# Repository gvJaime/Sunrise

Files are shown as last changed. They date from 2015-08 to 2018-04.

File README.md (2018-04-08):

# Sunrise Project

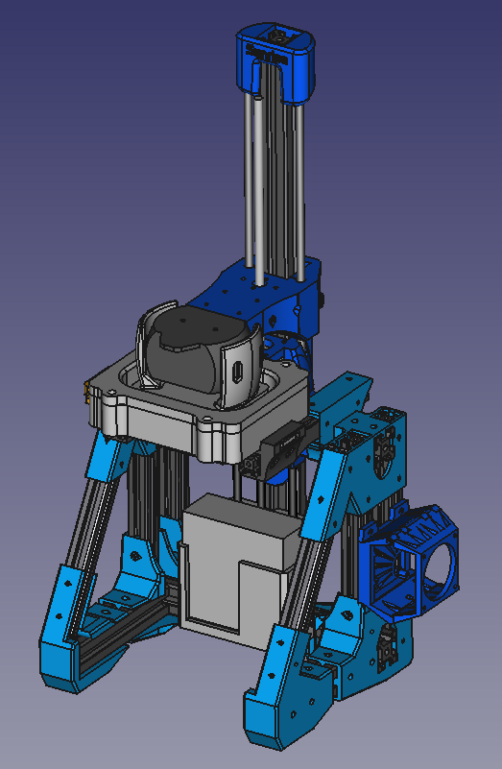
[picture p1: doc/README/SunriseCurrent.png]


## Introduction

The Sunrise Project is a research project, that aims to design an Open Source  hackable DLP based 3D printing system.

## Approach
The intention is to make the machine accesible to the general public. It must be sourceable, craftable, and modifiable by everyone. It aspires to be a platform for the community to explore this technology. Mechanics are scalable, source is available and modifiable, tools are open and obtainable.

## The technology

DLP 3D Printing uses photopolymierizing resin to craft the parts. Parts generate layer by layer as they are cured by a projector that outputs the cross-sections of the part, into the resin. There are various mechanical structures that can be used to achieve this.

This machine has what is called a _Bottom-Up_ structure. It has a vat, with transparent bottom, filled with resin. Underneath, an upward pointing DLP projector shoots light through the bottom window. The light striking on a **downward pointing** build surface cures the resin, forming a new layer.
Repeating this process, curing one layer below the previous one, ends up crafting the whole part, **upside down**.

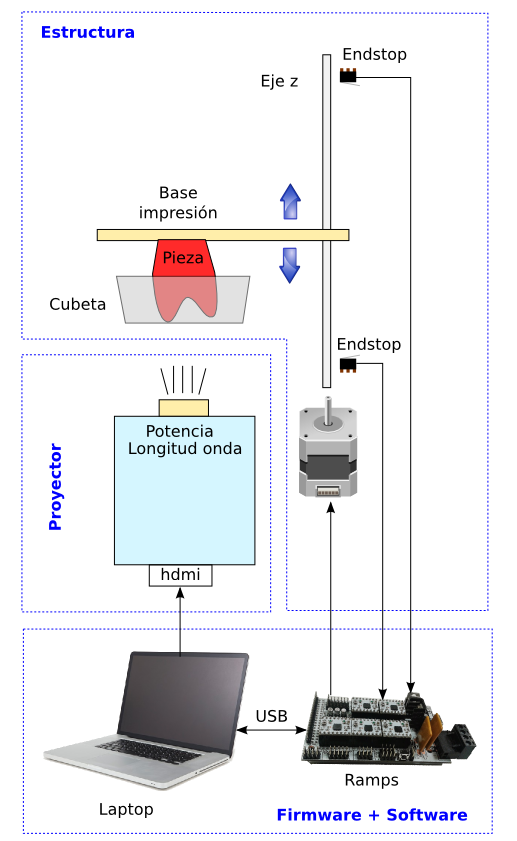
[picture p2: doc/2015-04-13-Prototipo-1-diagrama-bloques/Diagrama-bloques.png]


## The machine

This machine tries to stick to the RepRap philosophy, so structure and moving parts are 3D printed. Motion control is performed by an Arduino with a CNCShield, running a version of [GRBL][GRBL-link] that can be found [here][Sunrise-fw].
The projector is an [Optoma ML750][Optoma-link], with hacked optics for nearer focus.
PDMS based vat and flexible bottom vat system are being considered.

## About this repo

This repo contains the mechanical structure source. The tool of use is FreeCAD.
Folder content is descripted below
* `src`: Source files and assembly.
* `Step`: Step files for CAD import.
* `stl`: stl files for 3D printing.
* `FEM`: Part file duplicates for possible FEM analysis.
* `Fonts`: Fonts used in the design of the parts.
* `doc`: useful files for documentation
* `Software`: Provisional, holds useful software until it gets big enough for it to have its own repo.

### Cloning this machine

To build this machine, you need to print the 3D printable parts in [the stl folder][stlfolder]. You need to print each file once.

You will also need:
* 1958 mm of 20x20 aluminium extrusion profile
* 1378 mm of 30x30 aluminium extrusion profile
* Smooth rods, depending on desired Zaxis length
* Hammerhead nuts (Around 196 for 20x20 profiles and 52 for 30x30)
* DIN912 M4x8 bolts for 20x20 hammerhead nuts
* DIN912 M6x10 bolts for 30x30 hammerhead nuts
* 2 M3x10 Bolts
* 1 M3x20 Bolt
* 1 M3x30 Bolt
* A hacked Optoma ML750 (Focus moved forward with a M2 nut)

The length of the pieces of aluminium profiles and smooth rods can be seen in the [assembly file][Assembly]. Due to this being still in development there's not a lot of documentation. If you have any doubts [feel free to ask in the "issues" section][issue].

**Please note:** From v0.2.5 this repo uses [Assembly 2 FreeCAD workbench][Assembly2] for the assembly. You may want to install it before opening the assembly file.

### Contributing to this repo

You can contribute to this repo by forking it, and making pull requests to the [Development branch][Develop]. If you find problems to make the contribution this way, [place an issue][issue] and we'll work it out.

Due to FCStd files being unmergeable, Assembly.FCStd is modified only on the Development branch. It may not be included in pull requests. Remember that you need [Assembly 2 FreeCAD workbench][Assembly2] to open it.

In case of contributing using gitflow, take advantage of git diff features on FCStd files, and avoid big commit files, paste this lines on your ~/.git/config:
```
[include]
    path = ../.gitconfig
```
These will include the particular repo configuration, that tells git to unzip the files before diffing them.

## History

### Sunrise v0.3 (In development)

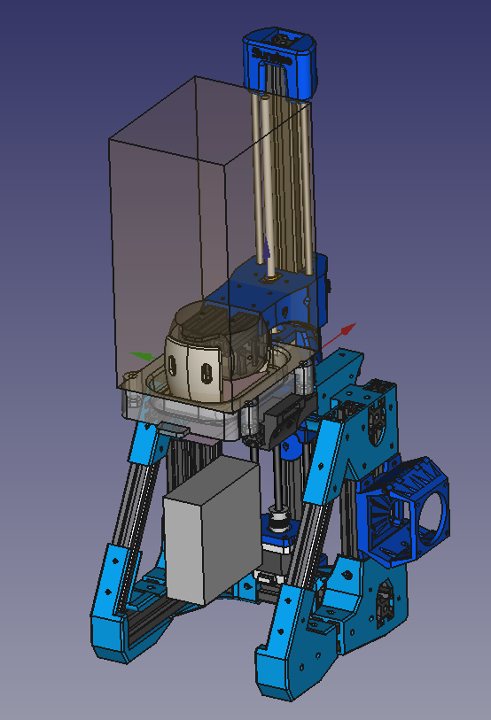
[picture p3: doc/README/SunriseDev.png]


#### Target Specs

* Easier assembly and printing.
* Build environment enclosure.
 * Must be compatible with fast vat swapping. (Vat may go out by pulling from it, rather than lifting it)
 * Zcarriage will access the environment through a bellow
 * Enclosure, VAT, and platform will come out as a whole, so uninstalling will be easier.
* Bellow for projector. UV light must not get out of the bellow.
* Proyector is placed sideways so the machine can be narrower
* Ball joint based autoleveling platform

### Sunrise v0.2.5

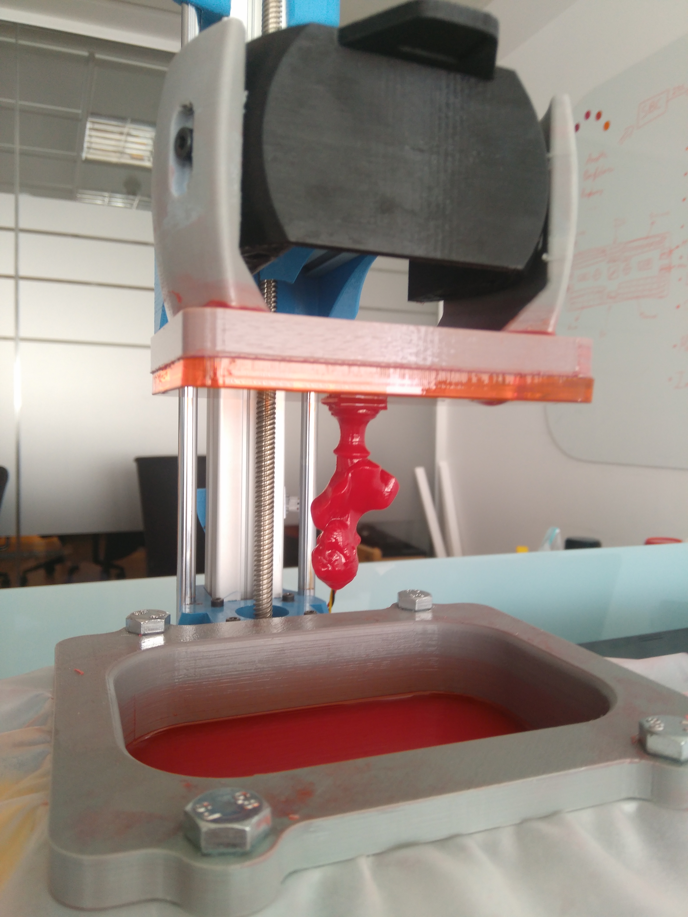
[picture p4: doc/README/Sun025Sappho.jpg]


####Changes
* Lower part of the frame redesigned
	* Easier assembly
	* Less bolt usage
	* Filaflex pads on legs

### [Sunrise v0.2 "Aluminium"][Sunrise-v0.2]

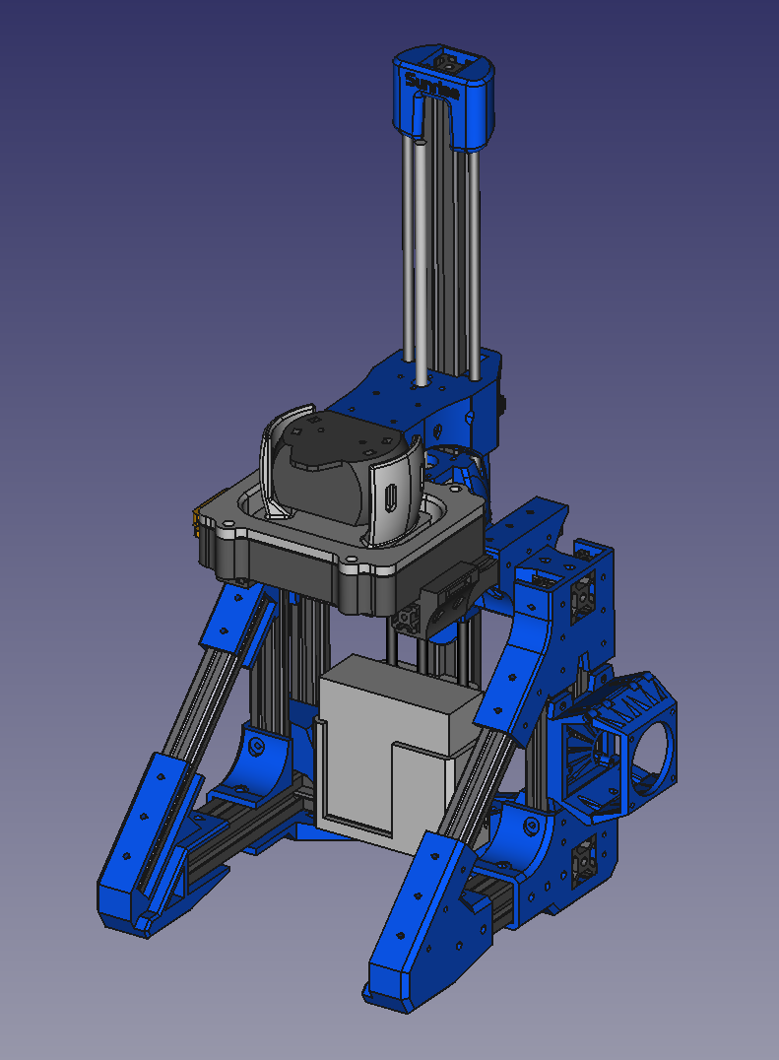
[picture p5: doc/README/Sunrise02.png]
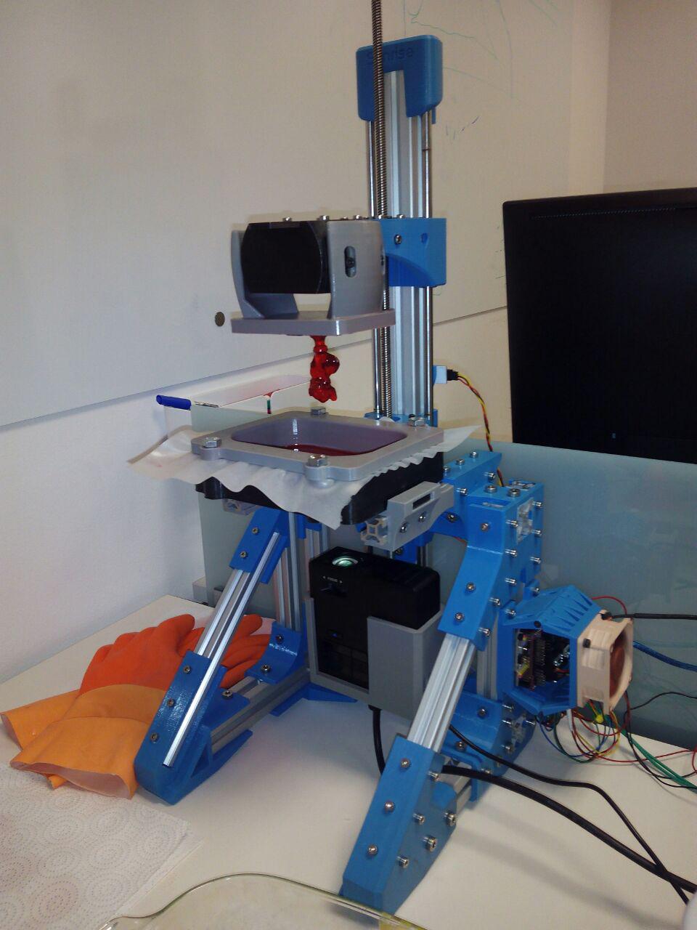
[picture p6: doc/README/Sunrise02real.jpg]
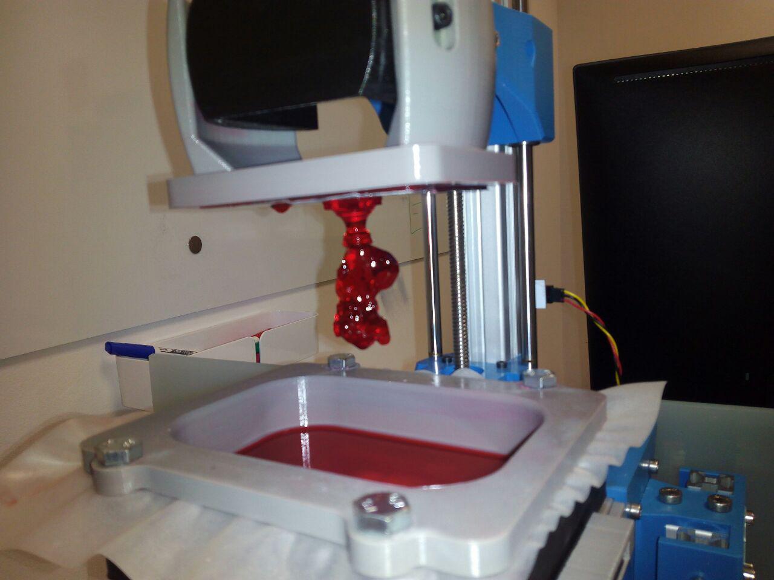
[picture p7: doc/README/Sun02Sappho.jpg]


#### Specs:
* Motor assisted projector axis for resolution adjustment.
* Aluminium extrusion profiles + printed parts based structure. Way more rigid than v0.1.
* Hacked [Optoma ML750][Optoma-link] pico-projector.
* Expandable design, able to hold several projectors.
* [Arduino UNO][AU-link] + [CNCShield][CNCS-link] + [a modified GRBL][Sunrise-fw] for motion control.
* [Creation Workshop][CW] as slicer and projector control.
* QuickFit for easy replacement of the vat.

### [Sunrise v0.1 "Mendelian"][Sunrise-v0.1]

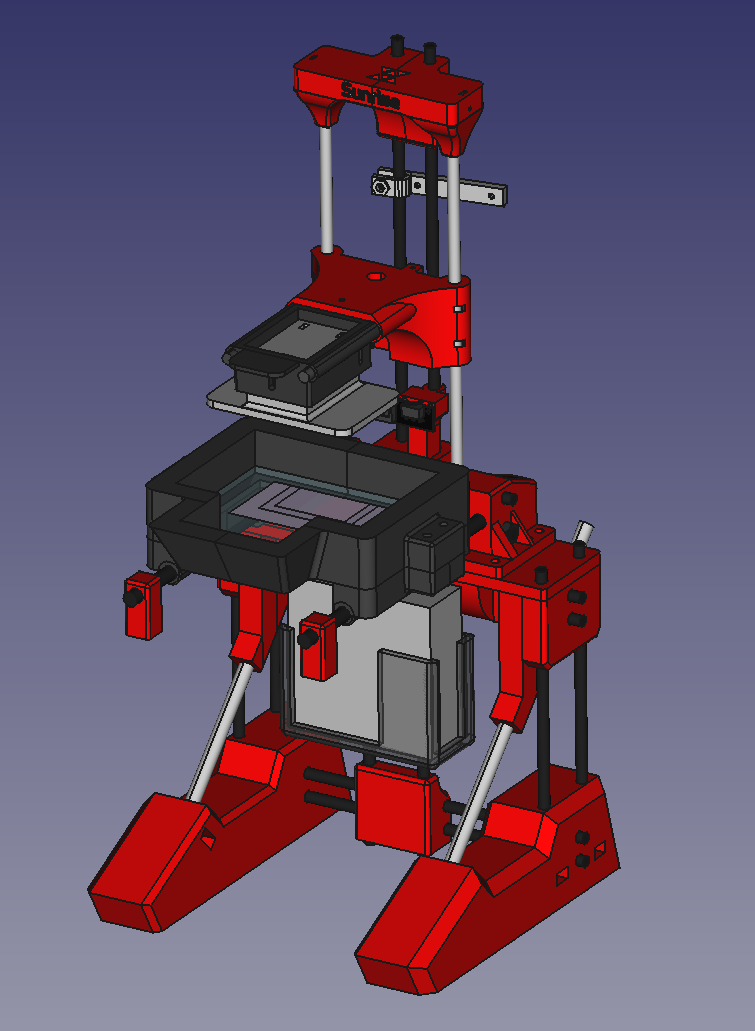
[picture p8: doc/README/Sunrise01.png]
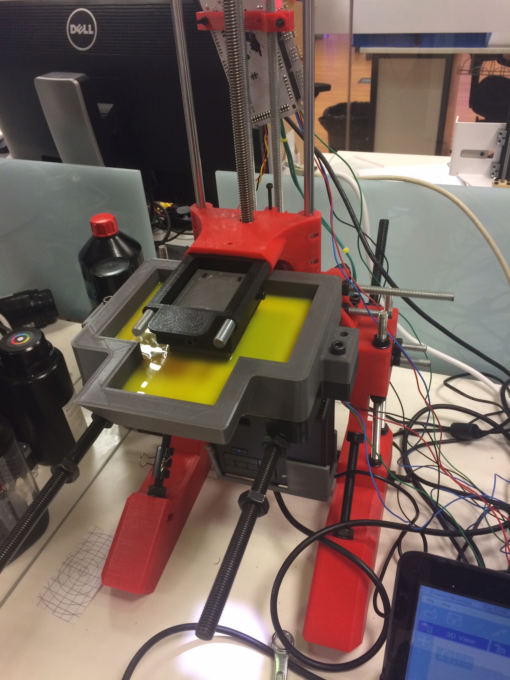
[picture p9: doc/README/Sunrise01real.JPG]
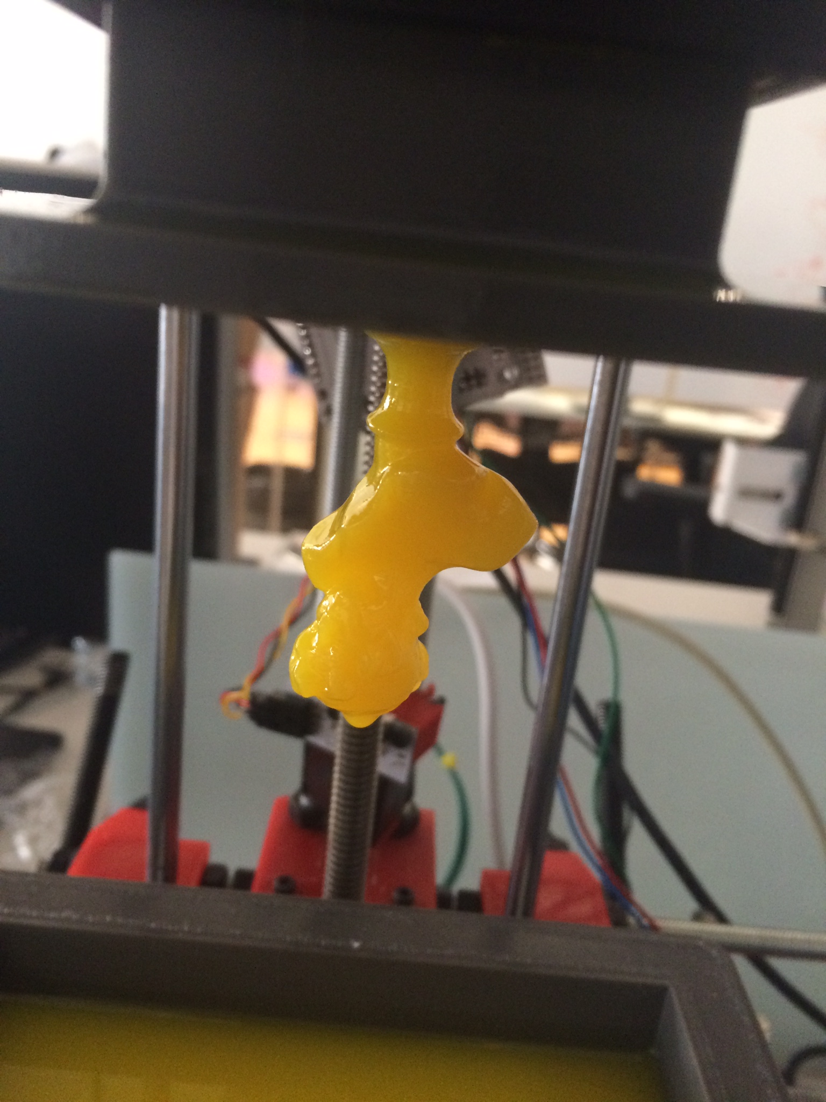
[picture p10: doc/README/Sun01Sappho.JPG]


#### Specs:
* Threaded rod + printed parts based structure.
* Hacked [Optoma ML750][Optoma-link] pico-projector used to save space.
* Modular setting for easy technique testing.
* [Arduino MEGA][AM-link] + [RAMPS][RAMPS-link] + [Marlin][Marlink] for motion control.
* [Creation Workshop][CW] as slicer and projector control.
* PDMS coated resin vat.

## Credits
To everyone with the courage to go open source and contribute to humankind's DLP 3D printing knowledge

* To Clone Wars Barcelona for [ResinCAT3D][Resincat]
* To the Eraikizpi team for [Eraikizpi][Erai]
* To [BuildYourOwnSLA][BYOSLA] forum
* Michael Joyce from B9Creations for [B9Creator][b9c]
* To EnvisionLabs, for [Creation Workshop][CW]
* To [Alessandro Ranelucci][alranel], for creating [Slic3r][slicer]
* To [Mundo Reader S.L.][bq], for sponsoring and financing this project from September 2014 to April 2016

Thank you

## License



This machine is licensed under a [Creative Commons Attribution-ShareAlike 4.0 International License](http://creativecommons.org/licenses/by-sa/4.0/). Please read the LICENSE files for more details.

Esta maquina tiene una licencia [Creative Commons Attribution-ShareAlike 4.0 International License](http://creativecommons.org/licenses/by-sa/4.0/). Por favor, lea los ficheros LICENSE para más detalles

[GRBL-link]: https://github.com/grbl/grbl
[Sunrise-fw]: https://github.com/bqlabs/Sunrise-fw
[Sunrise-v0.1]: https://github.com/bqlabs/Sunrise/releases/tag/0.1
[Sunrise-v0.2]: https://github.com/bqlabs/Sunrise/releases/tag/0.2
[slicer]: http://slic3r.org/
[bq]: https://bq.com
[alranel]: https://twitter.com/alranel
[CW]: http://www.envisionlabs.net/
[Marlink]: http://reprap.org/wiki/Marlin
[RAMPS-link]: http://reprap.org/wiki/RAMPS_1.4
[AM-link]: https://www.arduino.cc/en/Main/arduinoBoardMega
[AU-link]: https://www.arduino.cc/en/Main/arduinoBoardUno
[CNCS-link]: http://blog.protoneer.co.nz/arduino-cnc-shield/
[Optoma-link]: http://www.optomausa.com/projectordetails.aspx?PTypeDB=Business&PC=ML750
[BYOSLA]: http://www.buildyourownsla.com
[Erai]: http://reprap.org/wiki/Eraikizpi
[Resincat]: http://reprap.org/wiki/ResinCat_3D/es
[PTS]: http://reprap.org/wiki/ResinCat_3D_PTS
[b9c]: http://www.b9c.com/
[plates]: ./stl/plates
[Assembly]: ./DynamicAssembly.FCStd
[stlfolder]: ./stl
[issue]: https://github.com/bqlabs/Sunrise/issues/new
[Develop]: https://github.com/bqlabs/Sunrise/tree/Development
[Assembly2]: https://github.com/hamish2014/FreeCAD_assembly2

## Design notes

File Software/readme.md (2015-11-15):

 # Software:

 * 3dDLPUVController project from https://github.com/area515/UVDLPSlicerController
 * Printrun with cairoSVG from https://github.com/paclema/Printrun/tree/cairoSVG

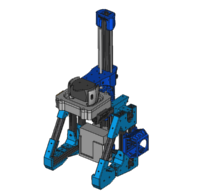
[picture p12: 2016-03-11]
doc/images/main.png

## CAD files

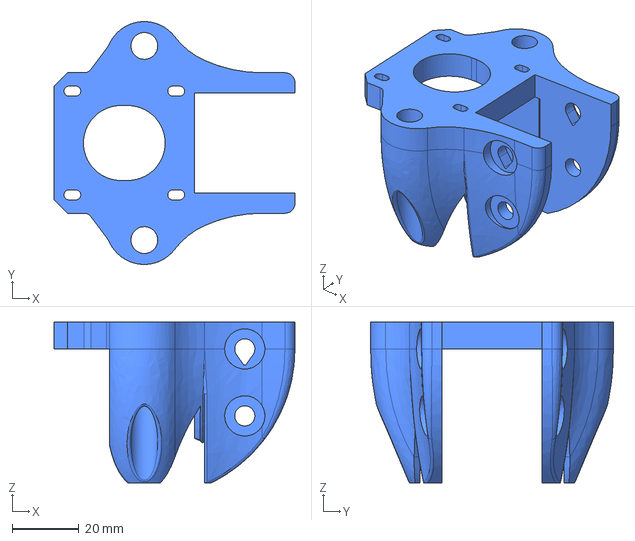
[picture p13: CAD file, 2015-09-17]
Step/ProjectorModule/ProjectorAxis/BaseToMainBeam.step
72.0 x 72.5 x 48.0 mm

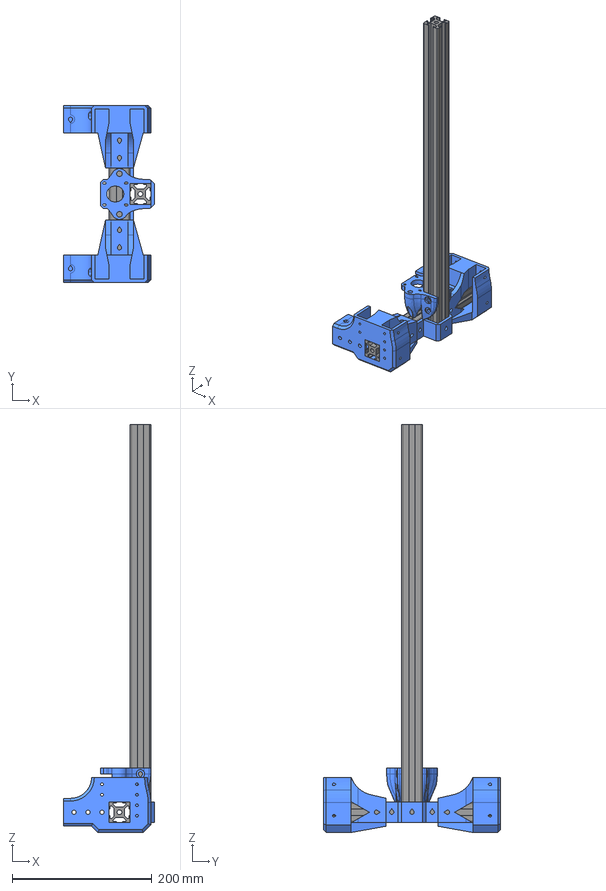
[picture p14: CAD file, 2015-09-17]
src/ProjectorModule/MainFrame/MainBeamLowFix.fcstd
130.0 x 254.0 x 584.0 mm
LeftAnkle
Clone of T slot extrusion 30x30x254
T slot extrusion 30x30x570
RightAnkle
BaseToMainBeam
MainBeamLowFix

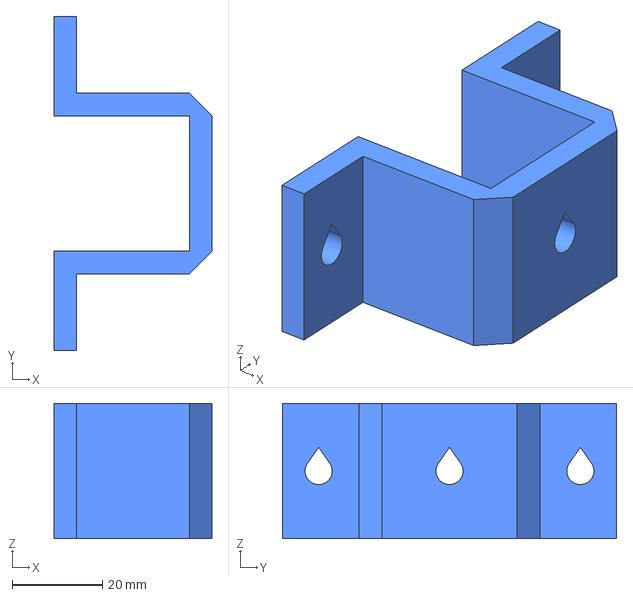
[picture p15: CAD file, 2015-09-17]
Step/ProjectorModule/MainFrame/MainBeamLowFix.step
35.0 x 74.0 x 30.0 mm

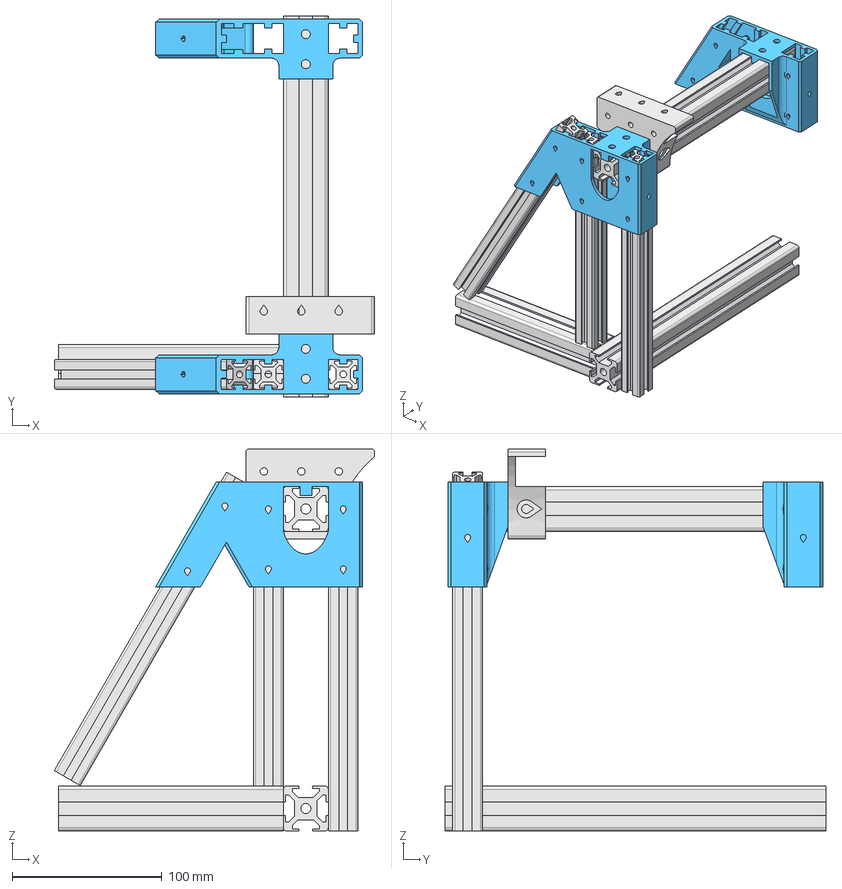
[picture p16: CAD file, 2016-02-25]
src/ProjectorModule/MainFrame/UpperNode.FCStd
213.9 x 254.0 x 255.0 mm
Reference
RUpperNode
RUpperNode (Mirror #5)

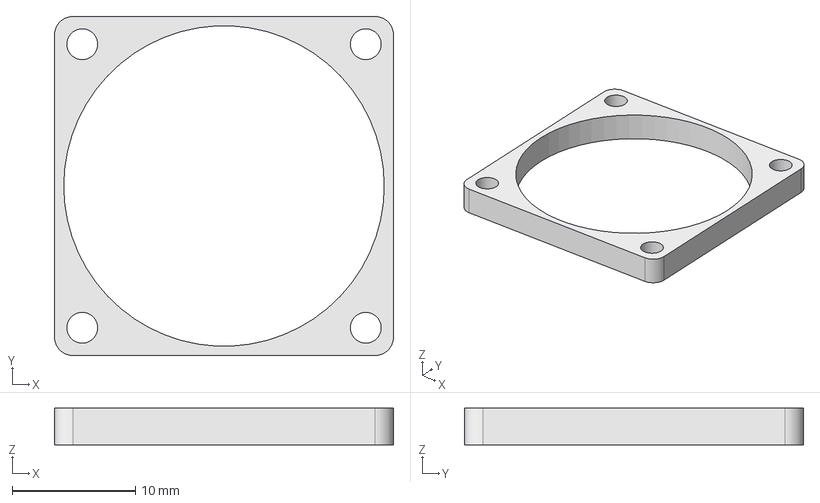
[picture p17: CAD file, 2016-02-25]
src/ProjectorModule/OptomaML750_hacked/Spacer.fcstd
27.5 x 27.5 x 3.00 mm

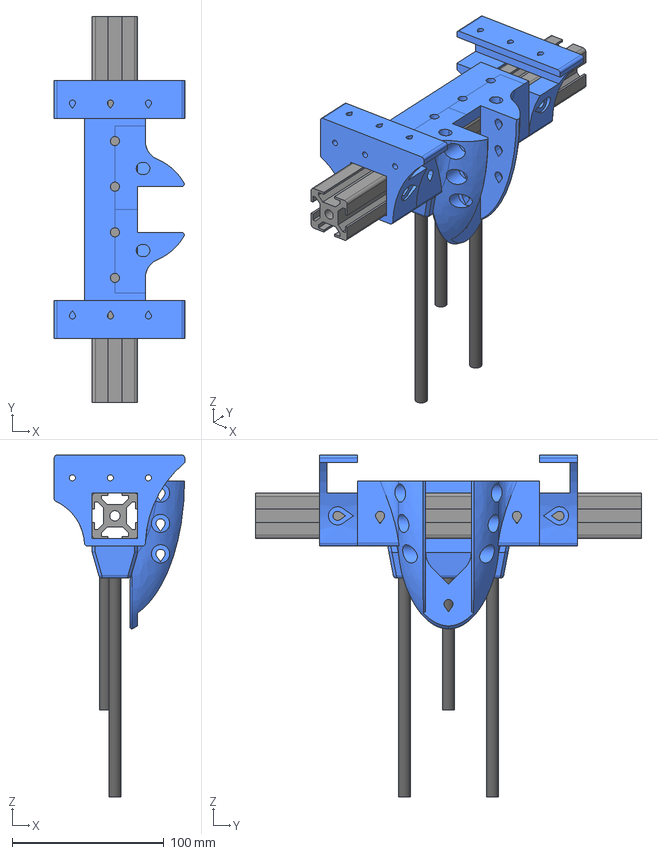
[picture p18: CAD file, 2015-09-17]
src/ProjectorModule/ProjectorAxis/UpperRailHold.fcstd
86.0 x 254.0 x 225.0 mm
SmoothRod002
CenterNode
RVATbarHolder
LVATbarHolder
Clone of T slot extrusion 30x30x254 001
ThrRod
SmoothRod003
UpperRailHold

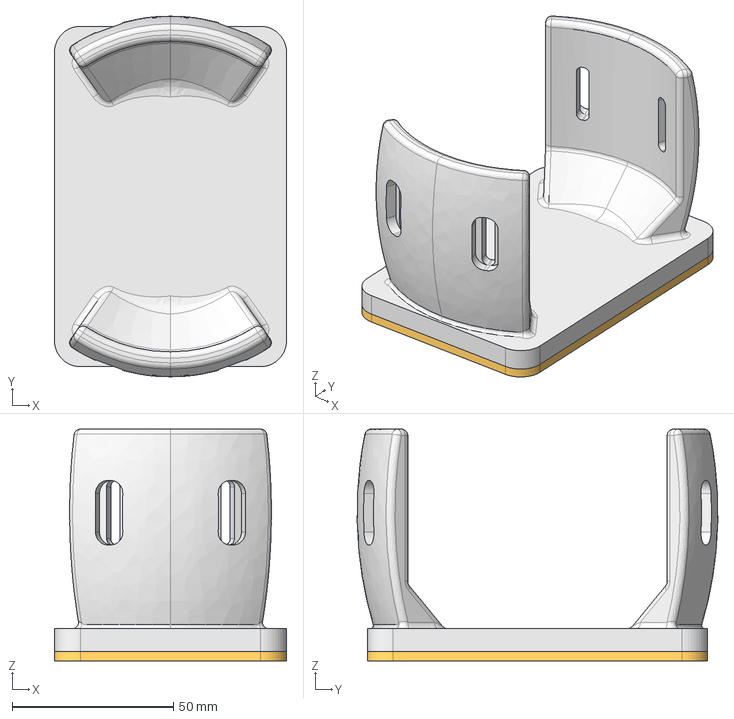
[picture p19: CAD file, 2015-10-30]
src/ZAxisModule/Platform/BuildSurface.fcstd
72.0 x 111.9 x 72.0 mm
Platform
BuildSurface

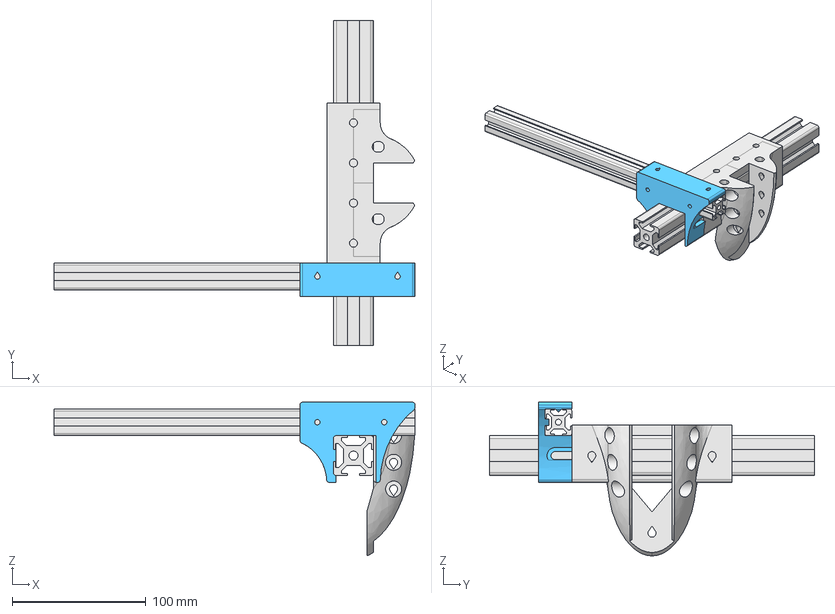
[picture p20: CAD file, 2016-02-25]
src/ZAxisModule/VATbarHolder.fcstd
270.0 x 243.0 x 115.0 mm
T slot extrusion 30x30x243 001
T slot extrusion 20x20x270 001
CenterNode
VATbarHolder

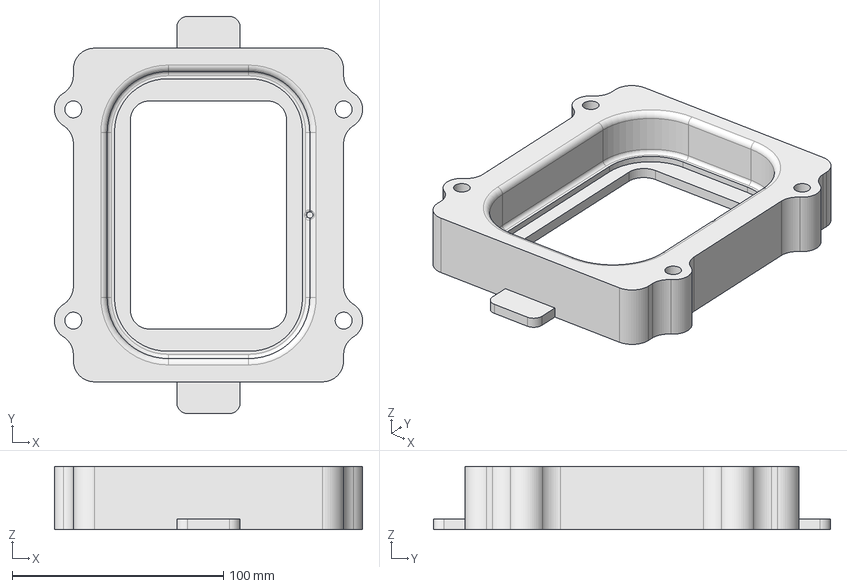
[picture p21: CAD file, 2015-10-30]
src/ZAxisModule/VATs/FlexiVAT/FlexiVATBase.fcstd
146.0 x 188.0 x 30.0 mm

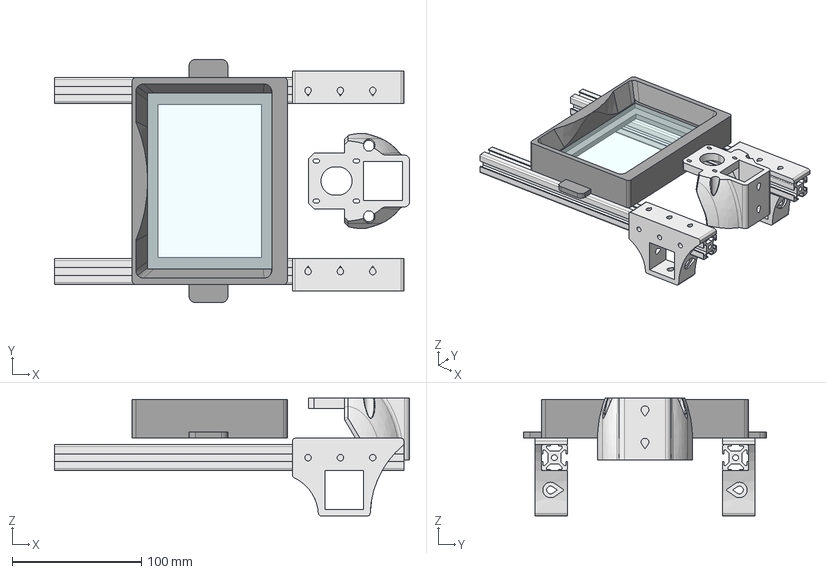
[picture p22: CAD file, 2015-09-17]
src/ZAxisModule/VATs/PDMSVAT/PDMSVAT.FCStd
274.4 x 188.0 x 91.0 mm
T slot extrusion 20x20x270 002
T slot extrusion 20x20x270 001
Glass001
LeftVATbarHolder
RightVATbarHolder
NEMAmount
PDMSVAT

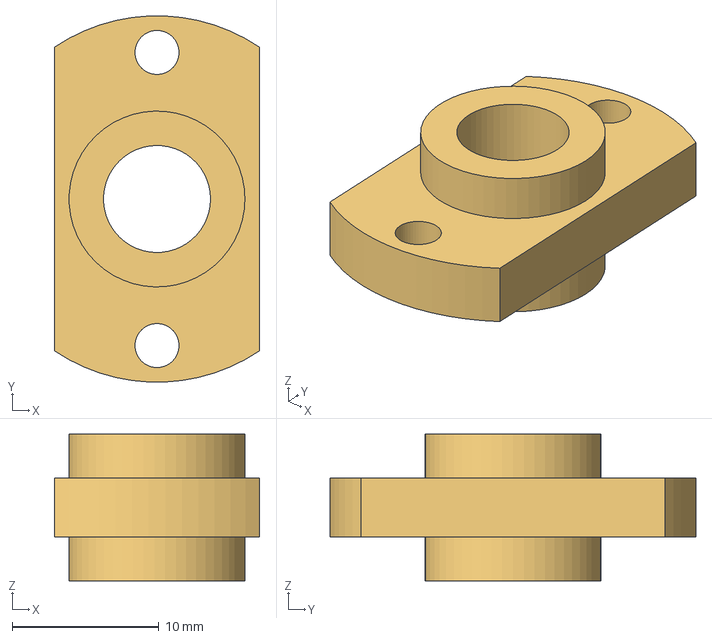
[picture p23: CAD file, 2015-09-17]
src/ZAxisModule/Zcarriage/4Starts2Profiles/SpindleNut.fcstd
14.0 x 25.0 x 10.0 mm

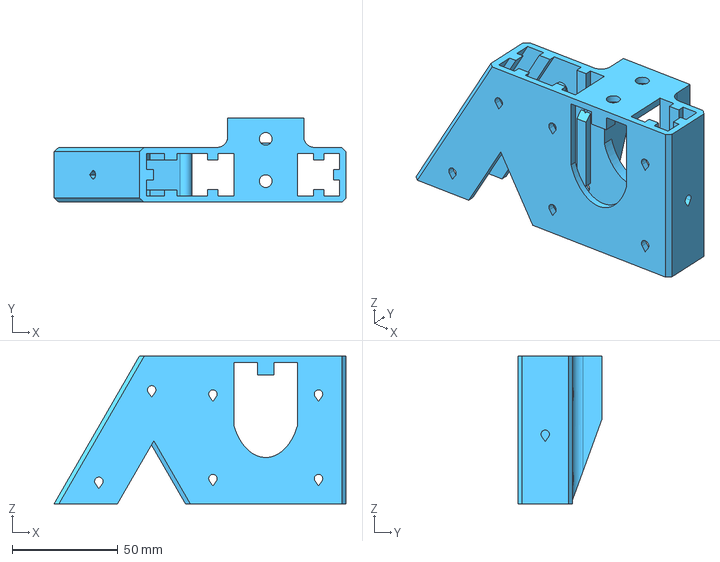
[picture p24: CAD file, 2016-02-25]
Step/ProjectorModule/MainFrame/UpperNode.step
138.2 x 40.0 x 70.0 mm

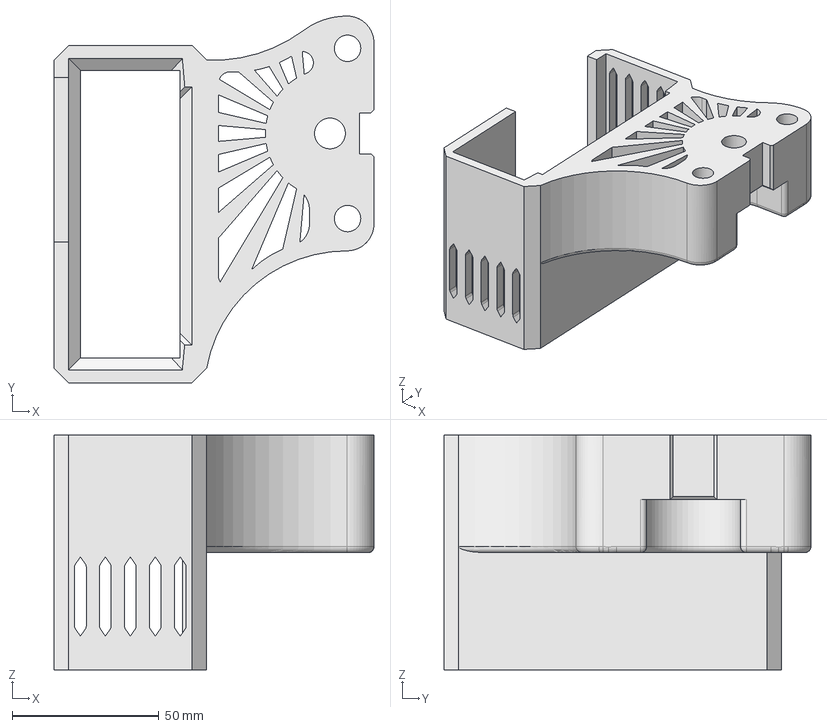
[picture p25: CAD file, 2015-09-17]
Step/ProjectorModule/OptomaML750_hacked/HacktomaAdaptor.step
109.0 x 125.0 x 80.0 mm

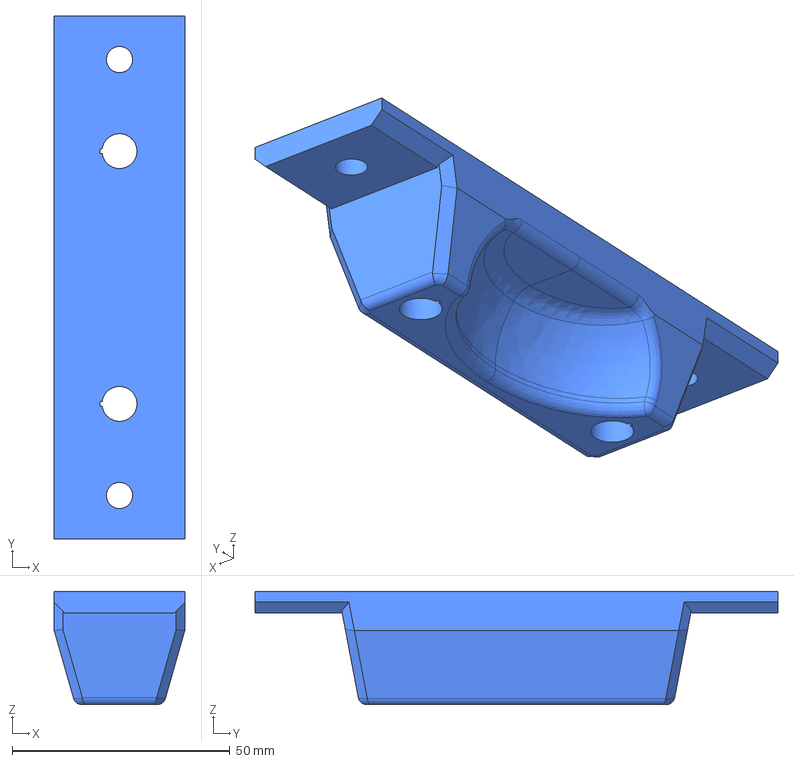
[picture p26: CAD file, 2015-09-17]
Step/ProjectorModule/ProjectorAxis/UpperRailHold.step
30.0 x 120.0 x 26.0 mm

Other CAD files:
Step/ZAxisModule/VATbarHolder.step
Step/ZAxisModule/VATs/FlexiVAT/FlexiVATTop.step
Step/ZAxisModule/VATs/PDMSVAT/PDMSVAT.step
Step/ZAxisModule/Zcarriage/Zcarriage_4S_2P.step
Step/ProjectorModule/MainFrame/ElecHolderLower.step
Step/ProjectorModule/MainFrame/ElecHolderUpper.step
Step/ProjectorModule/MainFrame/LowerNodeAnkle.step
Step/ProjectorModule/MainFrame/LowerNodeTip.step
Step/ZAxisModule/CenterNode.step
Step/ZAxisModule/EndstopHolder.step
Step/ZAxisModule/LVATHolder.step
Step/ZAxisModule/M8 nut.stp
Step/ZAxisModule/NEMA.step
Step/ZAxisModule/NEMAMount.step
Step/ZAxisModule/Platform.step
Step/ZAxisModule/PlatformHold.step
Step/ZAxisModule/QuickFit.step
Step/ZAxisModule/RVATHolder.step
Step/ZAxisModule/SpindleNut.step
Step/ZAxisModule/VATs/FlexiVAT/FlexiVATBase.step
Step/ZAxisModule/VATwithGlass.step
Step/ZAxisModule/upperZhold.step
src/ProjectorModule/MainFrame/ElecHolderUpper.fcstd
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

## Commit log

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2015-04-14 Z axis made longer, like in the physical mockup.
    [SunriseAssembly.FCStd]
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2015-04-14 Added the upper nodes of the Optoma Adaptor
    [SunriseAssembly.FCStd, UpperNode.FCStd, UpperNodeL.step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]
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2015-04-15 OptomaAdaptor collisions with other parts corrected by nice yet dangerous chamfers.
    [OptomaAdaptor.FCStd, OptomaAdaptor.step, SunriseAssembly.FCStd]
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2015-04-15 Made a fixing to the carriage on Optoma Adaptor
    [OptomaAdaptor.FCStd, OptomaAdaptor.step]
2015-04-15 Rail supports made shorter, so the rail can be longer.
    [ProjRailSupLabel.step, ProjRailSupLower.step, ProjRailSupport.FCStd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]
2015-04-15 New parts and details added to the assembly
    [SunriseAssembly.FCStd]
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2015-04-16 Methacrylate window for the vat dxf file added
    [Glass.dxf]
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2015-04-20 Tolerance added to the projector carriage rail
    [ProjectorCarriage.FCStd, ProjectorCarriage.step]
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2015-04-21 A modified version of the Prusa Hephestos z-axis-endstop holder has been added.
    [z-axis-endstop-hephestos.fcstd, z-axis-endstop-hephestos.step]
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2015-04-27 Endstop aperture made bigger so it doesnt break
    [z-axis-endstop-hephestos.fcstd, z-axis-endstop-hephestos.step]
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2015-05-05 Modified the platform hold, to be reinforced with two M8 threaded rods.
    [PlatformHold.step, PlatfromHold.FCStd]
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2015-05-05 Work done on Zcarriage M8 reinforcement, still unfinished.
    [Zcarriage.FCStd]
2015-05-06 Threaded rod reinforcements added to the ZCarriage
    [Zcarriage.FCStd, Zcarriage.step]
2015-05-06 Threaded rods moved to comply with Zcarriage previous geometry.
    [PlatformHold.step, PlatfromHold.FCStd]
2015-05-06 Changes added to the assembly. Checked for collisions.
2015-05-06 Thermal failure led to a NEMAmount revision, NEMA fixing bolt position corrected.
    [NEMAMount.step, NEMAmount.FCStd]
2015-05-06 Tie holds in Zcarriage corrected.
    [Zcarriage.FCStd, Zcarriage.step]
2015-05-06 Reinforcement in PlatformHold made thicker.
    [PlatformHold.step, PlatfromHold.FCStd]
2015-05-06 Added new Zcarriage design, that uses the witbox spindle. Still unfinished.
    [Zcarriage.FCStd, Zcarriage4thread.FCStd, ZcarriageWitbox.FCStd]
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2015-05-11 Fixed the missing platform fix bolt
    [ZcarriageSpinWitbox.FCStd]
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2015-05-11 Steppers kept deactivating after a minute. That's not a problem now.
    [Configuration_adv.h]
2015-05-12 Spindle hold fixing bolts kept colliding against the endstop. Bolt holes lenght increased.
    [SpindleHold.step, ZcarrSpinWitbox.step, ZcarriageSpinWitbox.FCStd]
2015-05-13 NEMA alignment fail prevention added
    [NEMAmount.FCStd]
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2015-05-19 Tinkered with Hacktoma Adaptor tolerances
    [HacktomaAdaptor.FCStd]
2015-05-19 Another iteration on HacktomaAdaptor. Made shorter, and placed further away from the rail.
    [HacktomaAdaptor.FCStd, HacktomaMount.step]
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2015-07-20 Add missing bolt on LowerNodeAnkle
    [LeftAnkle.step, LowerNodeAnkle.FCStd, RightAnkle.step]
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2015-07-20 Attempt at making the CenterNode design, which holds the Z axis to the lower frame
    [CenterNode.fcstd]
2015-07-21 Make first version of CenterNode, that holds the main vertical profile to the lower structure
    [CenterNode.step]
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2015-07-21 Redesign CenterNode to comply the new Zaxis structure. Now it can hold the 2 smooth bars in place
    [CenterNode.step]
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2015-07-22 Begin to make the NEMAmount design. It holds the Z axis NEMAmotor, and the smooth bars in place
    [NEMAmount.FCStd]
2015-07-23 FInish NEMAmount design conception by adding the vertical profile fixings, and refine the shape.
    [NEMAMount.step, NEMAmount.FCStd]
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2015-07-24 VAT fixing placement modified, Center Node modified to act as place definer
    [CenterNode.fcstd, CenterNode.step]
2015-07-24 Front bolt turned upside down, properly oriented. Warning: Step file has missing front face
    [CenterNode.fcstd, CenterNode.step]
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2015-07-27 Fix missing face by using igs format
    [CenterNode.fcstd, CenterNode.igs]
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2015-07-28 Finish the VAT bar holder design. It will hold the bars that support the VAT over the projector.
    [LeftVATbarHolder.step, RightVATbarHolder.step, VATbarHolder.fcstd]
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2015-07-28 Set VAT and projector positions, thinking about where the resolution axis and NEMA are going to be
    [HacktomaAdjustable.step]
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2015-07-29 Make clearance between the QuickFit flap and housing, so it is possible to remove the VAT
    [QuickFit.fcstd, QuickFit.step, VAT.FCStd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]
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2015-07-29 Make new VAT folder reorganisation so it contemplates various types of VATs
    [PDMSVAT.FCStd, PDMSVAT.step]
2015-07-30 Tinker with profiles, to decide how to reinforce the Z carriage
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2015-07-31 Fix the back bolts in NEMA mount, accidentally marked as 5mm deep
    [NEMAmount.FCStd]
2015-07-31 Add corrected NEMAmount into assembly
    [NEMAMount.step, NEMAmount.FCStd]
2015-08-03 Make design of the base of a flexible bottom VAT. Add a local assembly too.
    [FlexiVATAssembly.fcstd, FlexiVATBase.fcstd, FlexiVATBase.step]
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2015-08-03 Fix typos, and remove old files regarding the Platform
    [Platform.FCStd, PlatformH.step, PlatformHold.FCStd]
2015-08-03 Make new platform design, and repair some minor style issues on PlatformHold
    [Platform.FCStd, Platform.step, PlatformHold.FCStd]
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2015-08-03 Tilt the surfaces on the flap holder of the left VAT holder, so releasing the VAT is easier, or possible
    [LVATHolder.step, VATHolder.FCStd]
2015-08-03 Add the corrected left VAT holder into assembly
2015-08-04 Fix the missing nut holes in FlexiVATBase
    [FlexiVATBase.fcstd, FlexiVATBase.step]
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2015-08-04 Make the base of the projector carriage axis, which holds the NEMA
    [BaseToMainBeam.step]
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2015-08-05 Change all M5 bolts to M4 to comply with the extrusion profiles recently acquired
    [LVATHolder.step, LeftAnkle.step, LeftTip.step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]
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2015-08-05 Clean the sources of VATHolder, and restore lost draft operation. Add changes into assembly
    [LVATHolder.step, VATHolder.FCStd]
2015-08-05 Make BaseToMainBeam back holder shorter so a rigidizer part can fit underneath
    [BaseToMainBeam.step]
2015-08-05 Make part that fixes the main beam to the lower beam of the lower module main frame
    [MainBeamLowFix.fcstd, MainBeamLowFix.step]
2015-08-06 Make stl files of every single part designed in this new version so far
    [BaseToMainBeam.stl, CenterNode.stl, FlexiVATBase.stl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]
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2015-08-06 Redesign the center beam holder cut in CenterNode. Update stl and step files, and the assembly
    [CenterNode.fcstd, CenterNode.igs, CenterNode.step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]
2015-08-07 Make the design of the Zaxis endstop holder. Add changes into assembly
    [EndstopHolder.fcstd, EndstopHolder.step]
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2015-08-11 Make upper rail fix design for the projector axis. Add changes into assembly
    [UpperRailHold.fcstd, UpperRailHold.step]
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2015-08-14 Correct RollFix in Platform and PlatformHold, so it doesn't rotate that much.
    [Platform.FCStd, Platform.step, PlatformHold.FCStd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]
2015-08-14 Add corrected platform to assembly. Hacktoma 60 microns added and 40 microns turned into 45
    [SunriseAssembly.FCStd]
2015-08-14 Correct left VATholder flap slot, so the VAT can be tilted in order to be removed.
    [LVATHolder.step, VATHolder.FCStd]
2015-08-14 Add corrected left VATholder into assembly
    [SunriseAssembly.FCStd]
2015-08-19 Increase membrane clearance to 0.8mm in FlexiVATTop. Also, update some stl files for printing
    [FlexiVATTop.fcstd, FlexiVATTop.step, LVATHolder.stl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]
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2015-08-20 Make new FlexiVATTop, that pushes the silicone membrane down and applies tension to it. Add changes into assembly
    [FlexiVATTop.fcstd, FlexiVATTop.step, SunriseAssembly.FCStd]
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2015-08-21 Add stl files for the new FlexiVAT, the corrected PlatformHold, and the new HacktomaAdaptor
    [FlexiVATBase.stl, FlexiVATTop.stl, HacktomaAdaptor.stl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]
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2015-08-26 Make HacktomaAdaptor slot wider (106mm) and make place for the rear pads. This tackles issue #10. Changes added into assembly
    [HacktomaAdaptor.FCStd, HacktomaAdaptor.step, HacktomaAdaptor.stl]
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2015-08-28 Update RVATholder. Now it has a block that prevents the vat from turning around.
    [RVATHolder.step, RVATHolder.stl, VATHolder.FCStd]
2015-08-28 Redesign QuickFit so it fixed the vat when pulling from it. Also, another 623ZZ measures are being used
    [QuickFit.fcstd, QuickFit.step, QuickFit.stl]
2015-08-28 Make HacktomaAdaptor SmRod and Leadscrew holes bigger, so it lets the carriage move properly. This closes issue #19
    [HacktomaAdaptor.FCStd, HacktomaAdaptor.step, HacktomaAdaptor.stl]
2015-08-28 Add corrected HacktomaAdaptor into assembly
2015-08-31 Cut the flap holding pad in QuickFit, so it doesnt collide with RVATHolder when open. This closes issue #2
    [QuickFit.fcstd, QuickFit.step, QuickFit.stl]
2015-08-31 Add a bolt and a nut to fix the 623zz to QuickFit. This closes issue #3
    [QuickFit.fcstd, QuickFit.step, QuickFit.stl]
2015-08-31 Remove CenterNode's upper center bolts, they collided with the NEMA. Clean source file for better understanding, and modifiability. This closes #11 issue.
    [CenterNode.step, CenterNode.stl]
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2015-08-31 Make clearance for the CenterNode front bolt in HacktomaAdaptor. Do some minor folder organisation
    [HacktomaAdaptor(adjustable).FCStd, HacktomaAdaptor.FCStd, HacktomaAdaptor.step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]
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2015-09-02 Make chamfer on fixing bolts, so they can slip through the hole even though there is a wall blocking their way.
    [ElecHolderLower.step, ElecHolderLower.stl]
2015-09-02 Add the corrected HactomaAdaptor into assembly
2015-09-02 Make first design of the upper part of the Electronics holder. Correct color in ElecHolderLower.
    [ElecHolderUpper.fcstd]
2015-09-04 Make clearance for an allen key in ElecHolderLower, so the bolt is placeable and reachable
    [ElecHolderLower.step, ElecHolderLower.stl]
2015-09-04 Finish design of the upper part of the electronics case. Closing bolt position has been moved.
    [ElecHolderLower.step, ElecHolderLower.stl, ElecHolderUpper.fcstd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]
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2015-09-07 Fix broken 3d mesh generation in ElecHolderUpper
    [ElecHolderUpper.fcstd, ElecHolderUpper.step, ElecHolderUpper.stl]
2015-09-07 Add corrected ElecHolderUpper into assembly
2015-09-08 Correct leadscrew hole diameter. This closes issue #8. It is now 11 mm
    [HacktomaAdaptor.FCStd, HacktomaAdaptor.step, HacktomaAdaptor.stl]
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2015-09-14 Redesign PlatformHold. It now takes advantage of the extrusion profiles. Spherical outer surface guides the Platform leveling
    [PlatformHold.FCStd]
2015-09-14 Make a flap to hold the PlatformHold when releasing it from the carriage
    [PlatformHold.FCStd]
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2015-09-14 Place the tilt sphere surface center in a lower position in PlatformHold, so the platform can reach the bottom of the vat.
    [PlatformHold.FCStd]
2015-09-14 Make design of the Platform that can be leveled with the spherical surface guide
    [Platform.FCStd]
2015-09-14 Make step and stl files for the new Platform, PlatformHold, and Zcarriage
    [Platform.step, Platform.stl, PlatformHold.step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]
2015-09-14 Make nut lanes, hammerhead slots, and profile bolt holes wider in PlatformHold. Make spindle nut bolt closer together in Zcarriage.
    [PlatformHold.FCStd, PlatformHold.step, PlatformHold.stl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]
2015-09-14 Make nut lanes and profile nut holders wider. Add some tolerances.
    [PlatformHold.FCStd, PlatformHold.step, PlatformHold.stl]
2015-09-14 Turn spindle nut bolt holes into slots, so it can move freely and not jam the spindle
2015-09-14 Update Endstop holder design. Now it places the button in the middle of the machine
    [EndstopHolder.fcstd, EndstopHolder.step, EndstopHolder.stl]
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2015-09-16 Generate plates for Sunrise production with Witbox. Generate forgotten Zcarriage stl, and delete old gcodes
    [Zcarriage_4S_2P.stl, plate1.stl, plate2.stl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]
2015-09-17 Make the spherical surface ellipsoidal, so it can move vertically, allowing better platform homing
    [Platform.step, Platform.stl, PlatformHold.step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]
2015-09-17 Correct plate2 with duplicated UpperElecHolder
    [plate2.stl]
2015-09-21 Revert PlatformHold's outer surface back to spherical. Remove material from inside the sphere so profile nuts can be reachable
    [PlatformHold.step, PlatformHold.stl]
2015-09-21 Make Platform's inner surface cylindrical. Turn bolt holes into lanes, so height is adjusted by the own platform
    [Platform.step, Platform.stl]
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2015-09-25 Make a membrane holder pad, that squashes the membrane by all sides. Measures refer to local axes. Membrane clearance set to 0.6mm for the new silicone membrane
    [FlexiVATTop.fcstd, FlexiVATTop.step, FlexiVATTop.stl]
2015-09-25 Change Membrane tolerance to 0,4 mm
    [FlexiVATTop.fcstd, FlexiVATTop.step, FlexiVATTop.stl]
2015-09-25 Make indentation in FlexiVATBase so air in between the membrane and the glass can escape
    [FlexiVATBase.fcstd, FlexiVATBase.step, FlexiVATBase.stl]
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2015-10-09 Make MembraneCut deeper in FlexiVAT top so the membrane makes contact with the glass.
    [FlexiVATBase.fcstd, FlexiVATBase.step, FlexiVATBase.stl]
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2015-10-15 Fix holes in PlatformHold. Now nuts fit the lane, and stop in front of the bolt.
    [PlatformHold.FCStd, PlatformHold.step, PlatformHold.stl]
2015-10-20 FlexiVATTop may not fit in 20x20 plates
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2015-11-05 Fix Witbox stl plates
    [plate 4.stl, plate 5.stl, plate4.stl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]
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2016-02-06 Restyle UpperNode, relocate bolts, and turn printable bolts into tear shaped bolts
    [UpperNode.FCStd]
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
